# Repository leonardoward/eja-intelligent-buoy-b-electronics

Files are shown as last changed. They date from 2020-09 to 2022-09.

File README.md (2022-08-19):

# EJA Intelligent Buoy B with Ethernet - Electronic Design

Buoy B V2.0 integrates 4 main components (ESP32, LoRa, GPS and an Ethernet interface). It is a version of the previous Buoy B V1.0 but replaces the motor drivers with an Ethernet module.

This repository contains the KiCad design for the PCB of the Intelligent Buoy B. It also contains the 3D models used to visualize the design in the KiCad 3D viewer.

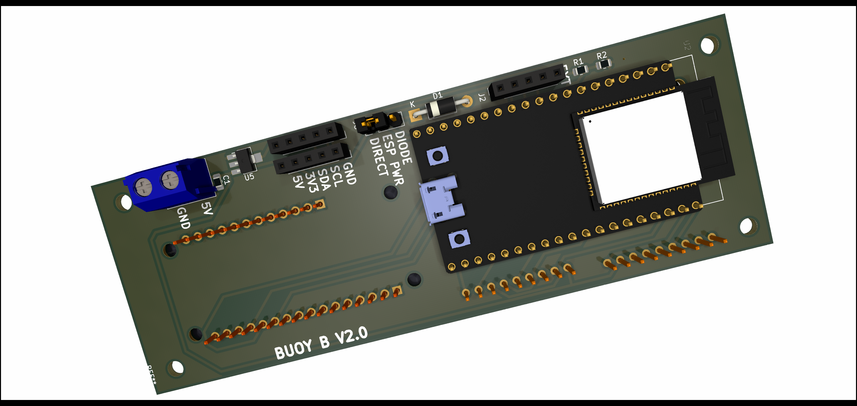
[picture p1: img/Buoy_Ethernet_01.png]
Front Layer PCB


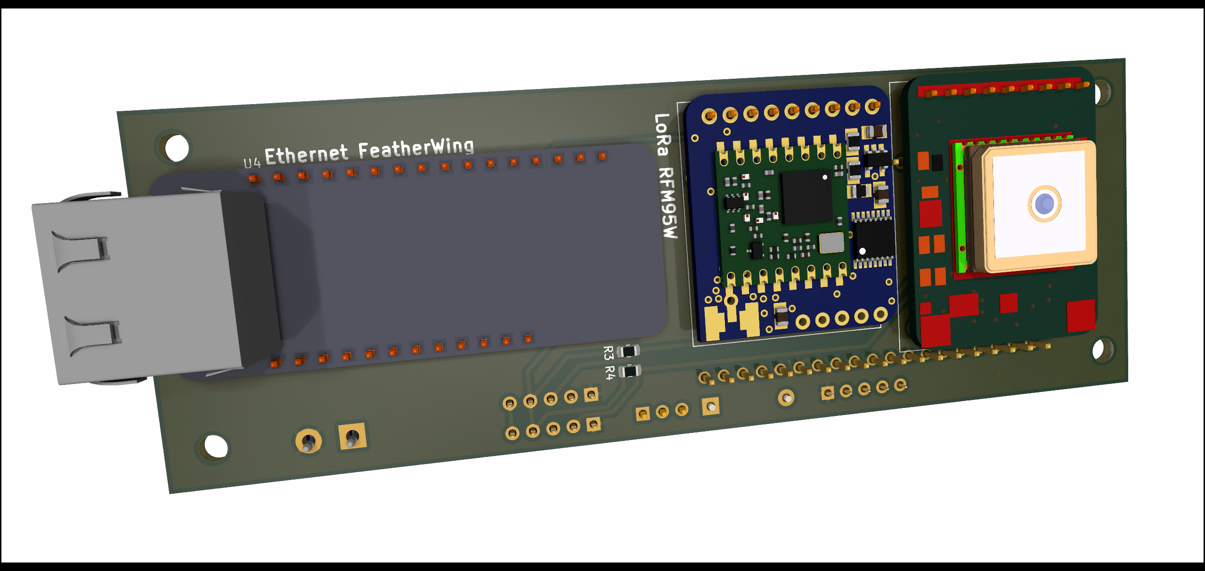
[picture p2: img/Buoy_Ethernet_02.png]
Back Layer PCB


## Main Components ##

- [ESP32-DEVKITC-32D](https://www.digikey.com/product-detail/es/espressif-systems/ESP32-DEVKITC-32D/1965-1000-ND/9356990)
- [RFM95W LoRa Radio](https://www.digikey.com/product-detail/es/adafruit-industries-llc/3072/1528-1667-ND/6005357)
- [TB6612FNG MOTOR DRIVER BOARD](https://www.digikey.com/product-detail/es/sparkfun-electronics/ROB-14450/1568-1755-ND/7915576)
- [Adafruit Ethernet FeatherWing](https://www.digikey.com/en/products/detail/adafruit-industries-llc/3201/6165788)

## Schematic ##

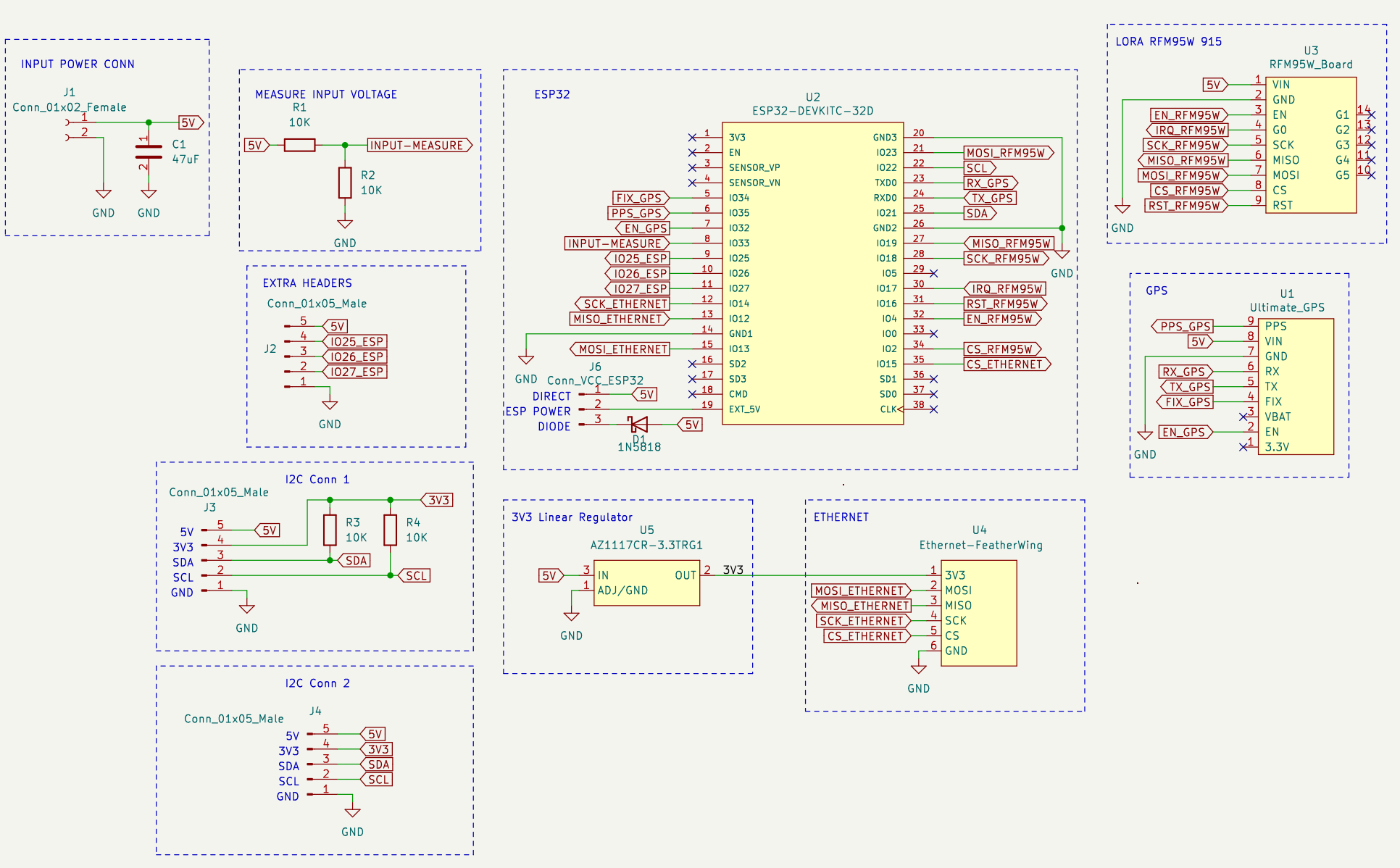
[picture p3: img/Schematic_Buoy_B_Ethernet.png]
Schematic


<!-- [For a detailed explanation of the schematic visit the following log.](https://hackaday.io/project/173457/log/181832-buoy-b-v10-schematic-and-pcb-design) -->

## PCB Layout ##

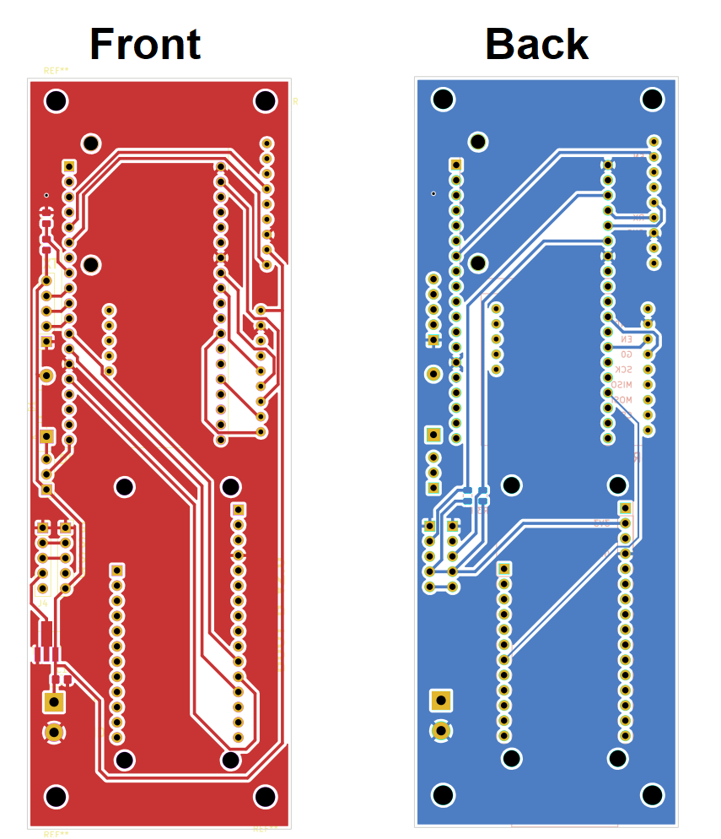
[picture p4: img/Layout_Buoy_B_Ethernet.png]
PCB Layout


## Assembly ##

Components List:

1. [ESP32-DEVKITC-32D](https://www.digikey.com/product-detail/es/espressif-systems/ESP32-DEVKITC-32D/1965-1000-ND/9356990)
2. [ETHERNET FEATHERWING](https://www.digikey.com/en/products/detail/adafruit-industries-llc/3201/6165788)
3. [CONN HDR 19POS 0.1 TIN PCB](https://www.digikey.com/product-detail/es/sullins-connector-solutions/PPTC191LFBN-RC/S7017-ND/810157)
4. [CONN HDR 9POS 0.1 GOLD PCB](https://www.digikey.com/product-detail/es/sullins-connector-solutions/PPPC091LFBN-RC/S7042-ND/810181)
5. [CONN HDR 9POS 0.1 GOLD PCB](https://www.digikey.com/product-detail/es/sullins-connector-solutions/PPPC091LFBN-RC/S7042-ND/810181)
8. PCB Buoy B V1.0
9. [CONN HDR 19POS 0.1 TIN PCB](https://www.digikey.com/product-detail/es/sullins-connector-solutions/PPTC191LFBN-RC/S7017-ND/810157)
10. [TERM BLK 2P SIDE ENT 5.08MM PCB](https://www.digikey.com/product-detail/es/on-shore-technology-inc/OSTTC022162/ED2609-ND/614558)
12. [CONN HDR 6POS 0.1 TIN PCB](https://www.digikey.com/product-detail/es/sullins-connector-solutions/PPTC061LFBN-RC/S7004-ND/810145)
13. [CONN HDR 5POS 0.1 GOLD PCB](https://www.digikey.com/product-detail/es/sullins-connector-solutions/PPTC051LFBN-RC/S6103-ND/807239)
14. [CONN HEADER VERT 3POS 2.54MM](https://www.digikey.com/product-detail/es/jst-sales-america-inc/S2B-XH-A-1-LF-SN/455-4226-ND/9961922)
15. [CONN HEADER VERT 3POS 2.54MM](https://www.digikey.com/product-detail/es/jst-sales-america-inc/S2B-XH-A-1-LF-SN/455-4226-ND/9961922)
16. [CONN HEADER R/A 3POS 2.5MM](https://www.digikey.com/product-detail/es/jst-sales-america-inc/S3B-XH-A-1-LF-SN/455-2954-ND/1556255)
17. Coin cell holder (included in [Adafruit Ultimate GPS](https://www.digikey.com/product-detail/es/adafruit-industries-llc/746/1528-1153-ND/5353613))
18. [Adafruit Ultimate GPS](https://www.digikey.com/product-detail/es/adafruit-industries-llc/746/1528-1153-ND/5353613)
19. CONN HDR 16POS 0.1 TIN PCB (included in [Adafruit Ultimate GPS](https://www.digikey.com/product-detail/es/adafruit-industries-llc/746/1528-1153-ND/5353613))
20. [RFM95W LoRa Radio](https://www.digikey.com/product-detail/es/adafruit-industries-llc/3072/1528-1667-ND/6005357)
21. CONN HEADER VERT 16POS 2.54MM (included in [RFM95W LoRa Radio](https://www.digikey.com/product-detail/es/adafruit-industries-llc/3072/1528-1667-ND/6005357))

<!-- [For a detailed Bill of Materials visit the following log.](https://hackaday.io/project/173457/log/183762-buoy-b-v10-bill-of-materials)

[For a detailed explanation about the soldering and assembly procedure visit the following log.](https://hackaday.io/project/173457/log/183666-buoy-b-v10-assembly) -->

<!-- ## Wiring Diagrams ##

### Battery Management ###

The original design of the board considered the following components:

- Battery (5V < Voltage < 15V)
- PCB Board Buoy B V1.0
- Buck Converter
- Switch
- Extra capacitor

![alt text](./Wiring_Diagrams/Wiring_Buoy_WithoutGSM_07_wired.png "Buck Converter")

Also, there is an alternative for the battery management, is possible to provide the required voltages with a boost converter and a 3.7V Battery, like the following example:

- 3.7V 1 Cell Battery
- PCB Board Buoy B V1.0
- Boost Converter
- Micro USB Breakout Board
- Switch
- Extra capacitor
- JST-XH 2 Pos female connector and a JST-XH 2 Pos male connector
- 5V Charger (only used to charge the battery)

![alt text](./Wiring_Diagrams/Wiring_Buoy_WithoutGSM_08_wired.png "Boost Converter")

This alternative is valid and possible, but is not ideal for longer working time (compared to the first one). It is important to consider the efficiency of the boost converter. The selected boost converter will have a voltage drop at a current higher than 500mA, that should be taken into consideration.

### Motors ###

The board was designed to handle 3 different types of motors, those are:

- Servo Motor

![alt text](./Wiring_Diagrams/Wiring_Buoy_WithoutGSM_06_wired.png "Servo Motor")

- Stepper Motor (using the driver TB6612FNG)

![alt text](./Wiring_Diagrams/Wiring_Buoy_WithoutGSM_09_wired.png "Stepper Motor")

- DC Motor (using the driver TB6612FNG)

![alt text](./Wiring_Diagrams/Wiring_Buoy_WithoutGSM_05_wired.png "DC Motor 1")

![alt text](./Wiring_Diagrams/Wiring_Buoy_WithoutGSM_05_wired_2.png "DC Motor 2")

[For more information about the wiring diagrams and the project visit the following log.](https://hackaday.io/project/173457/log/182722-buoy-b-v10-wiring-diagrams)

## Future improvements ##

[For more information about the recommended future improvements for the electronic design visit the following log.](https://hackaday.io/project/173457/log/183807-future-improvements-pcb-design) -->

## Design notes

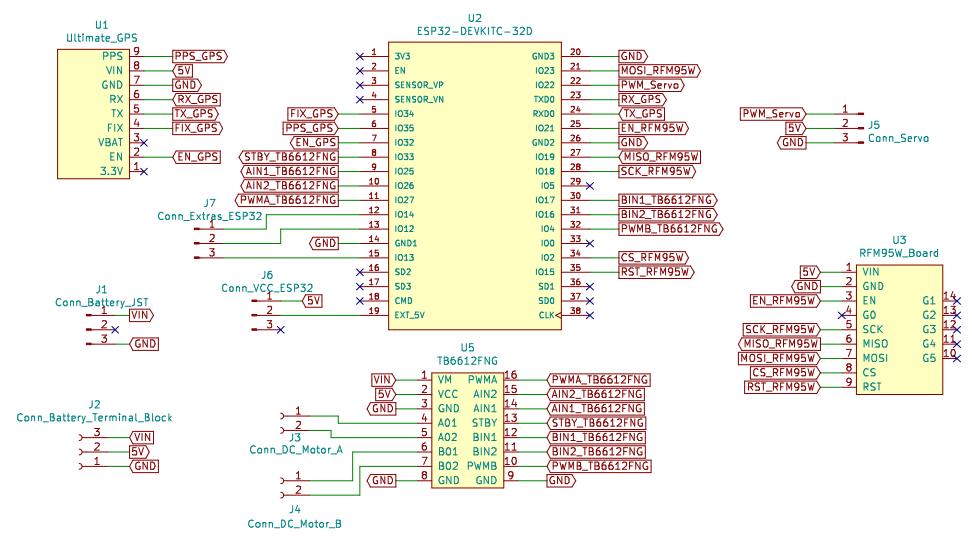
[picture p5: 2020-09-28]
img/Schematic_Buoy_B.png

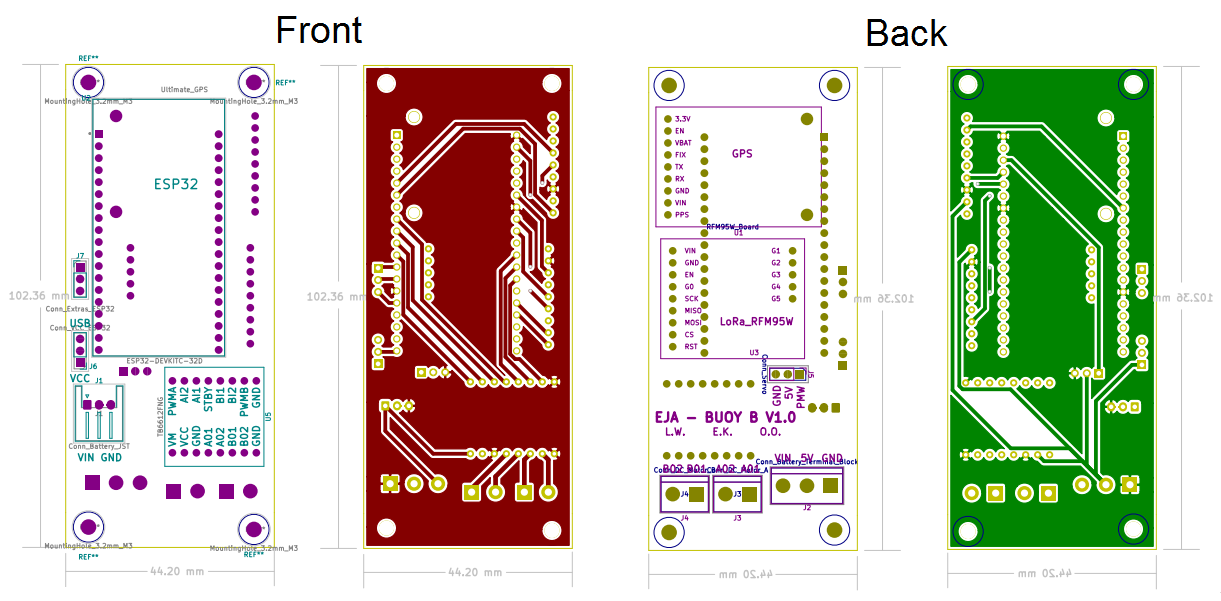
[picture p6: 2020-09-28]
img/Layout_Buoy_B.png

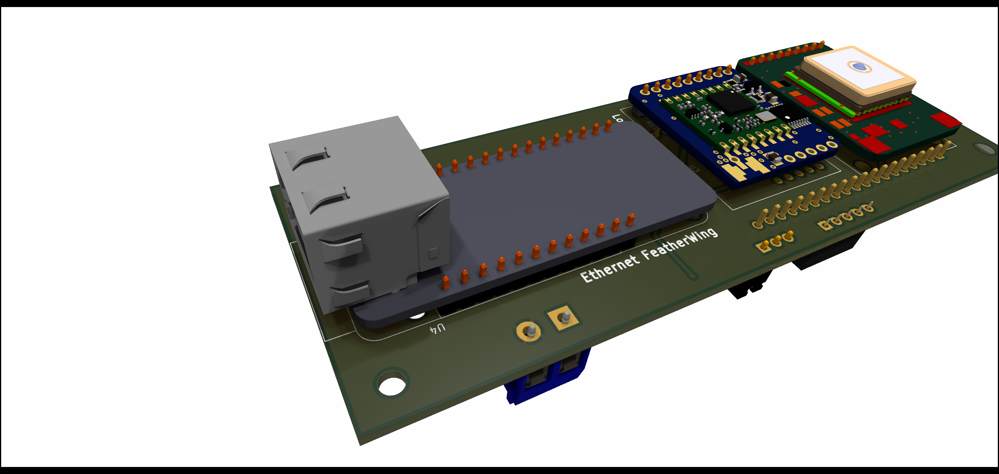
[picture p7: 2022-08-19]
img/Buoy_Ethernet_03.png

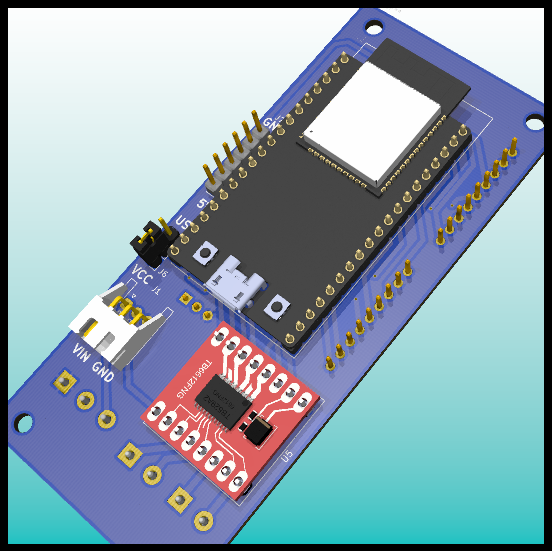
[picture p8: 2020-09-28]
img/Buoy_B_WithoutGSM_01.png

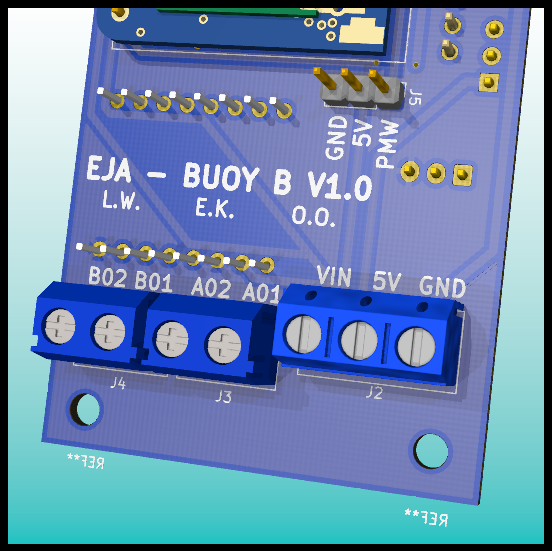
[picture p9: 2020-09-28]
img/Buoy_B_WithoutGSM_08.png

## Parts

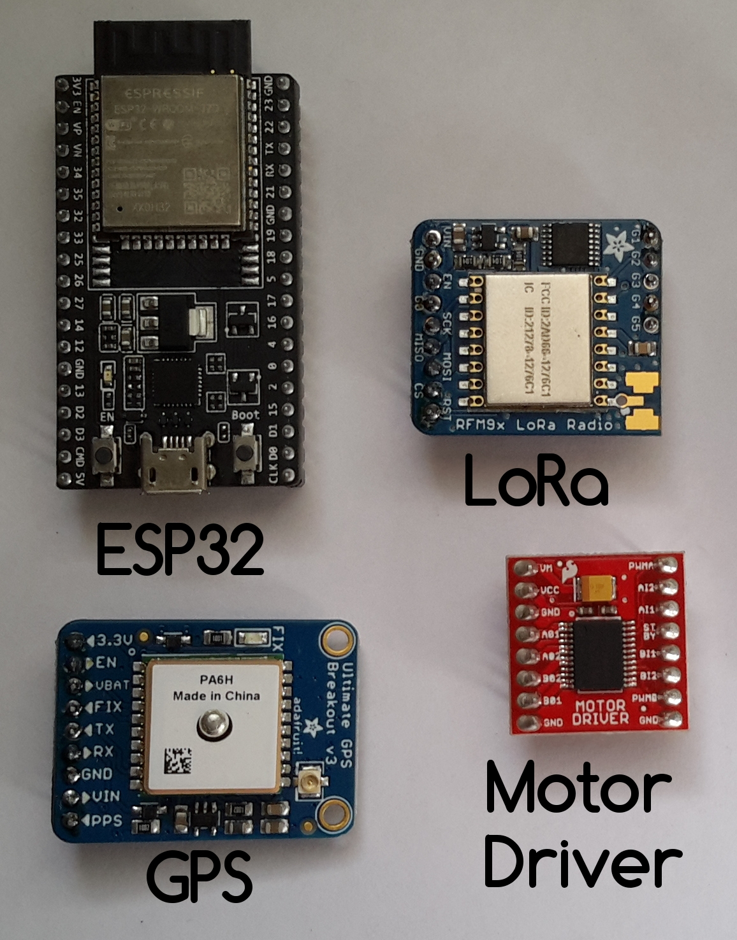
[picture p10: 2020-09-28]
img/Components_Buoy_B.jpg

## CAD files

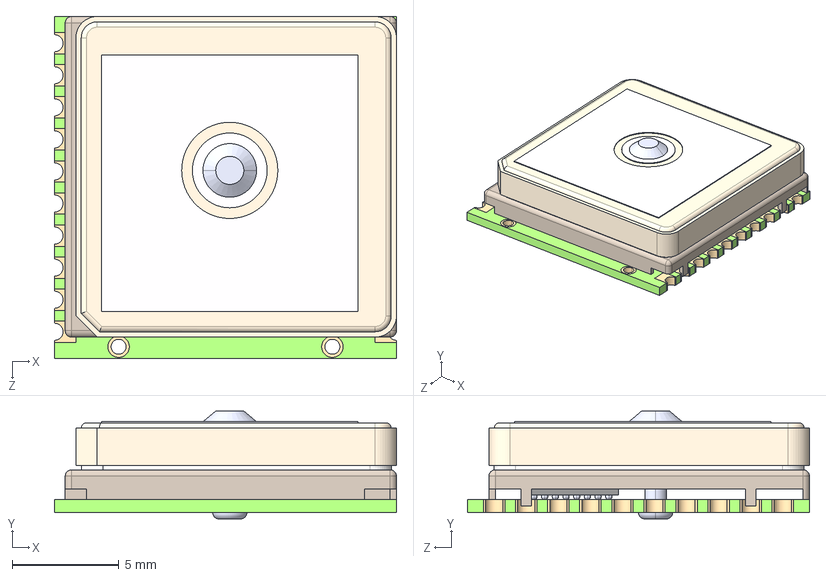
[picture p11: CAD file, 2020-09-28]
3D/PA6H Assembly.STEP
16.0 x 5.05 x 16.0 mm
PCB
VFBGA-64
RF Shield
Adhesive Pad
Ceramic Antenna
Rivet

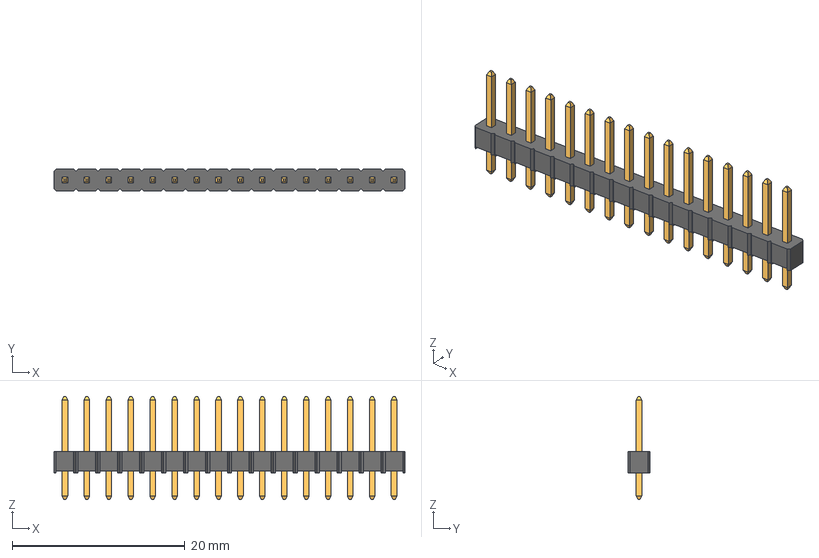
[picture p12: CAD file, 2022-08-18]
3D/16-Pin Header - Male - 2.54mm.step
40.6 x 2.54 x 11.9 mm

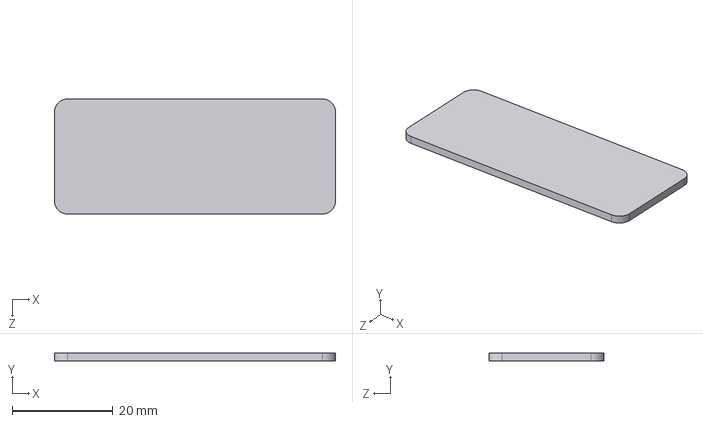
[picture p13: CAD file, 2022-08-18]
3D/Ethernet FeatherWing PCB.STEP
55.9 x 1.60 x 22.9 mm

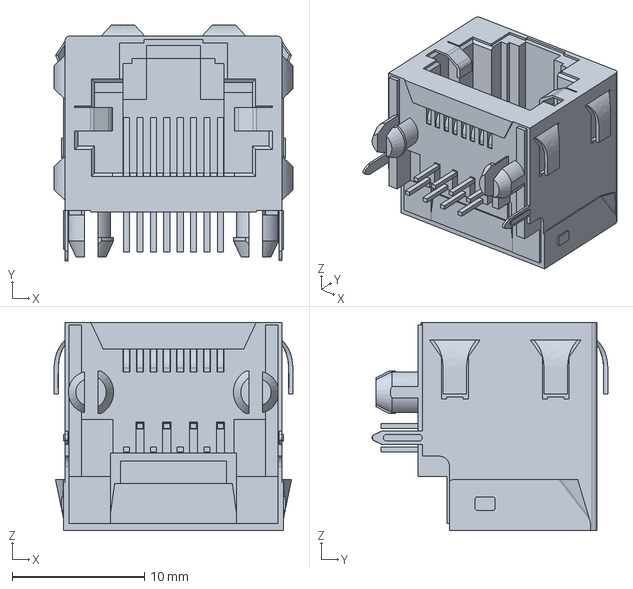
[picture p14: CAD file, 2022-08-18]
3D/ethernet connector.stp
18.0 x 17.8 x 15.7 mm

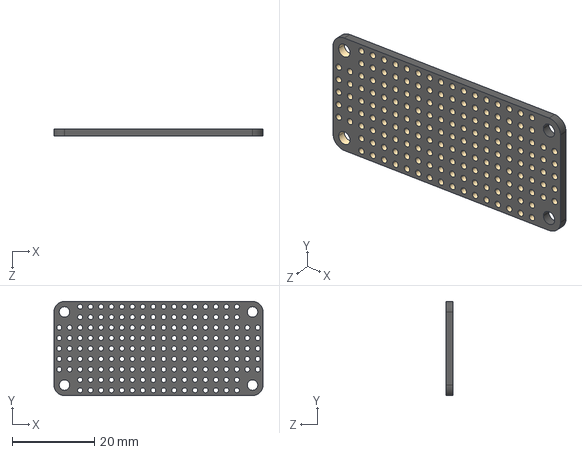
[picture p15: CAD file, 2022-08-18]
3D/FeatherWing Proto1.STEP
50.8 x 22.9 x 1.60 mm

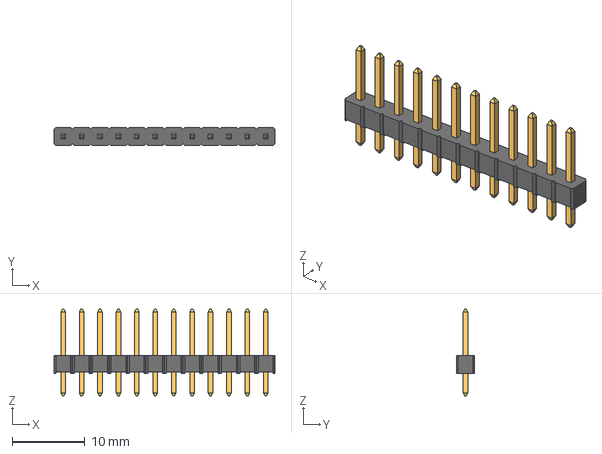
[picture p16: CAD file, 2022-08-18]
3D/12-Pin Header - Male - 2.54mm.step
30.5 x 2.54 x 11.9 mm

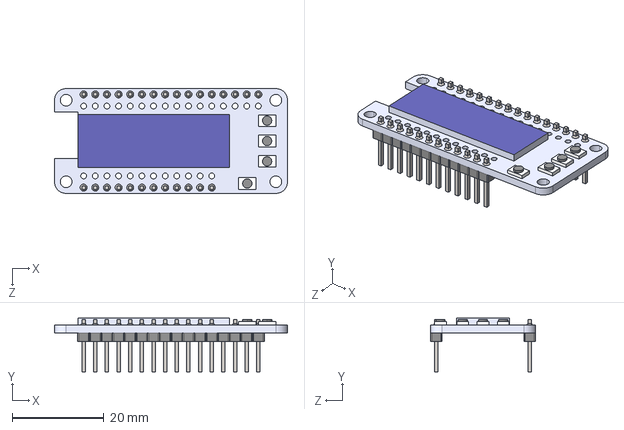
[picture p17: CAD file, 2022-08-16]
3D/Adafruit_Feather_Display032x128_000.STEP
50.8 x 11.7 x 22.9 mm

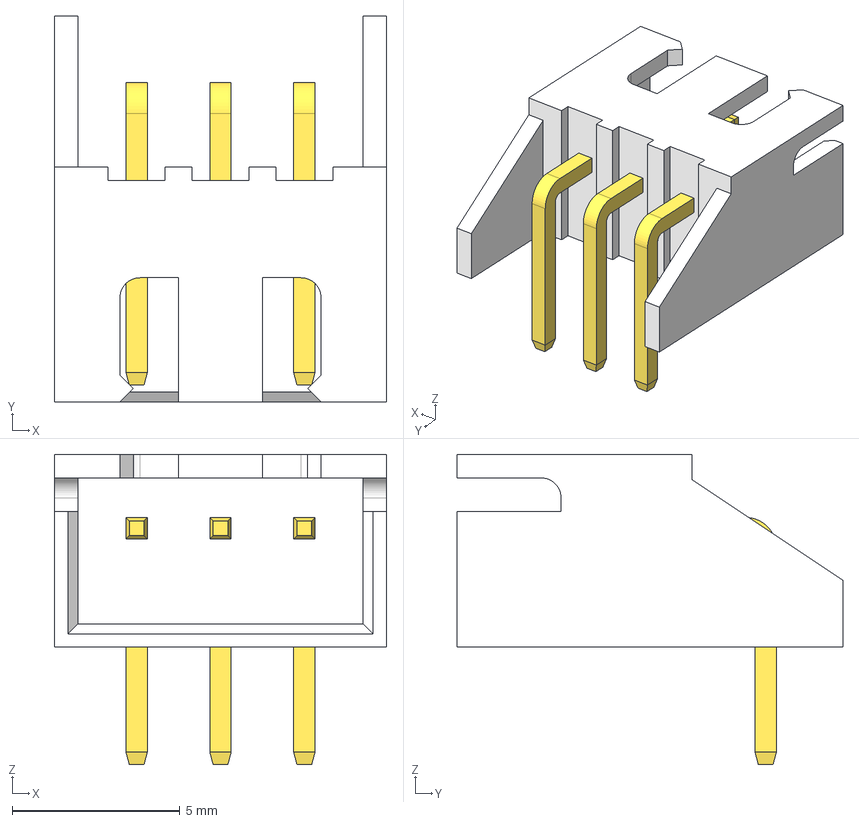
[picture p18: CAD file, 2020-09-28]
3D/S3B-XH-A.step
9.90 x 11.5 x 9.25 mm

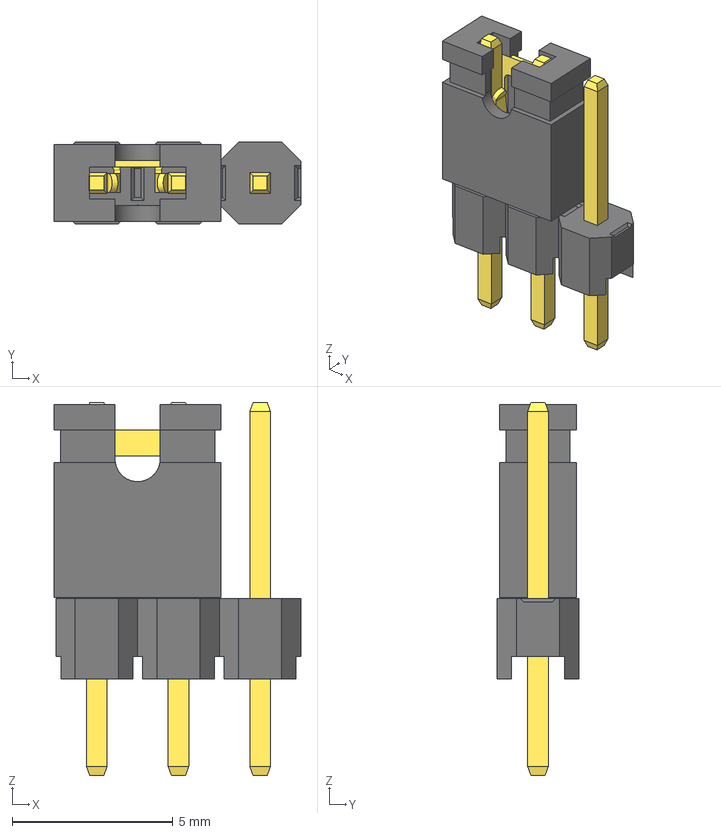
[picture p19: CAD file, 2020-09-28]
3D/Jumper3.step
7.68 x 2.54 x 11.6 mm

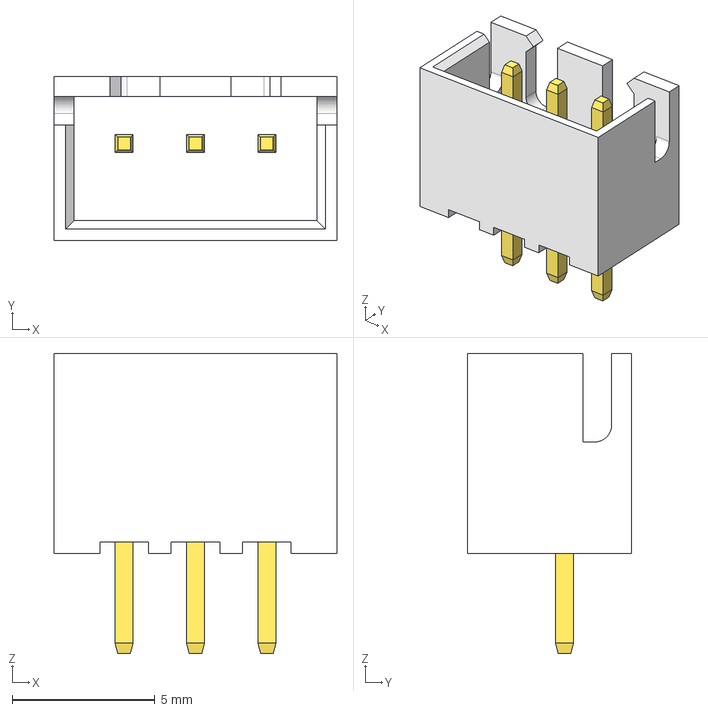
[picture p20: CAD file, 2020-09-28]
3D/B3B-XH-A.step
9.90 x 5.75 x 10.5 mm

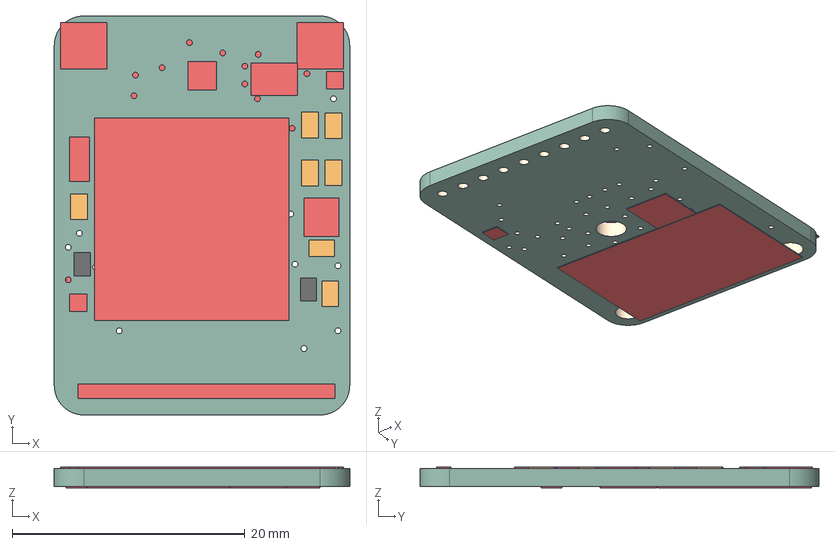
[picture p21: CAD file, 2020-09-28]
3D/Adafruit Ultimate GPS.step
25.4 x 34.3 x 1.77 mm
Board
FGPMMOPA6H
MIC5225-3.3
RED
10K x 7
MOUNTINGHOLE2.5 x 2
CUS520 x 2
CR1220
FIDUCIAL"" x 2
ADAFRUIT_2.5MM
U.FL
1X09_ROUND_70
PCBFEAT-REV-040
ADAFRUIT_5MM

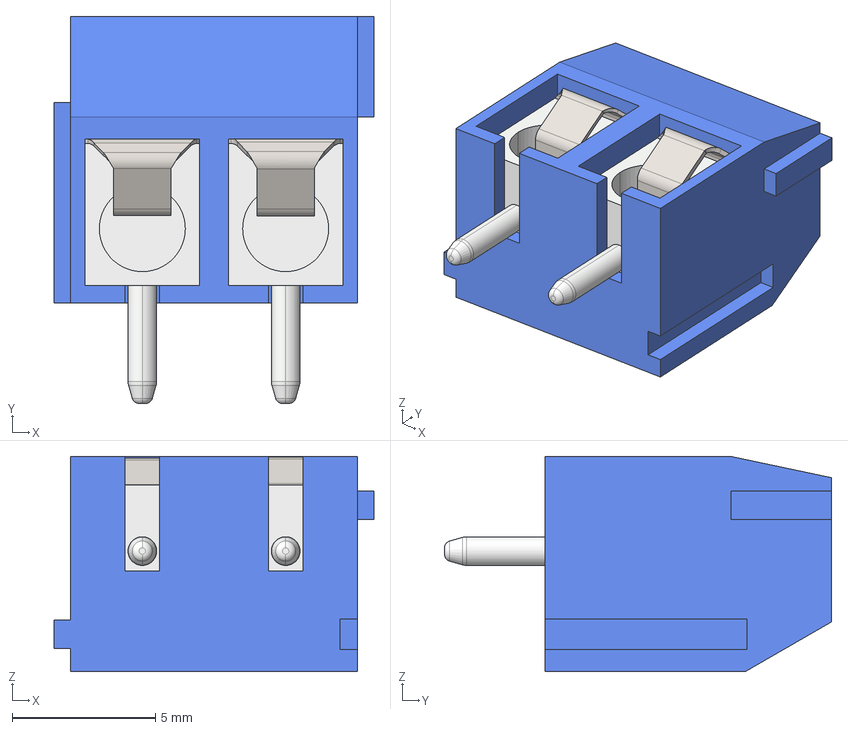
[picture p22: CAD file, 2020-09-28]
3D/TE_1776244-2.STEP
11.2 x 13.5 x 7.50 mm

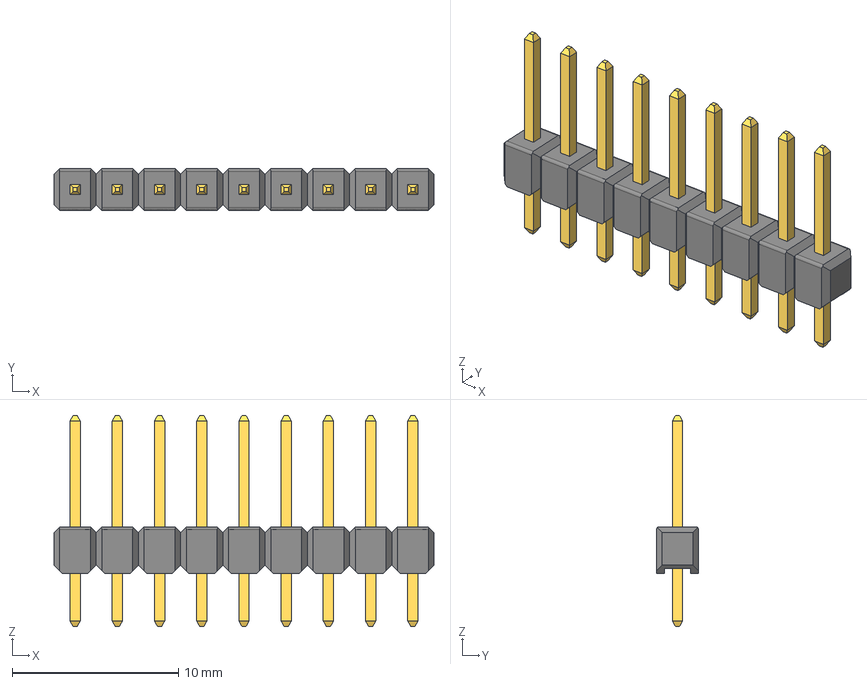
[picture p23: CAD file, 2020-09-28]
3D/Pin Header 1x9 TH Pitch 2.54mm.stp
22.9 x 2.54 x 12.7 mm

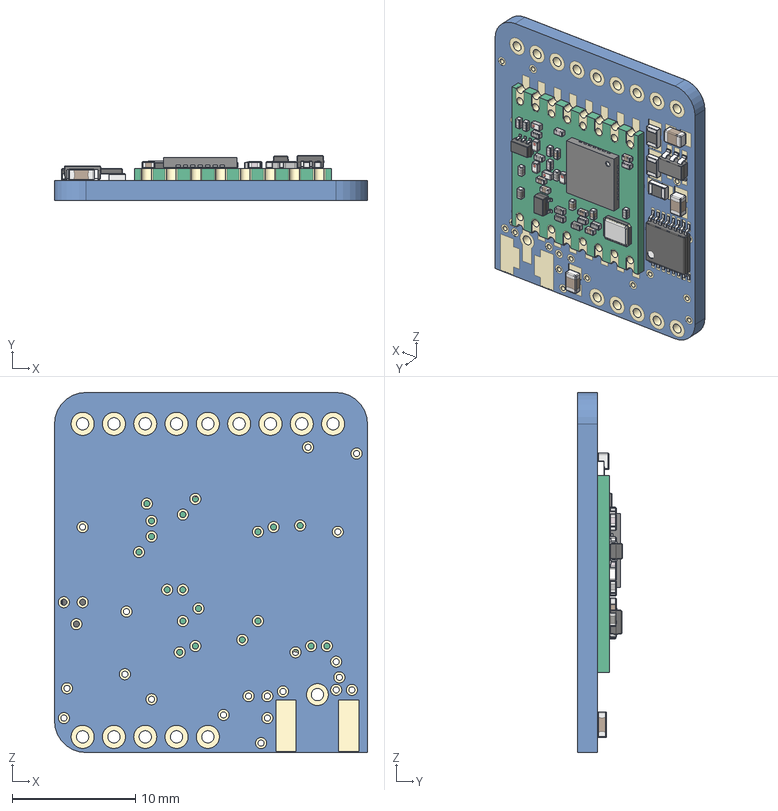
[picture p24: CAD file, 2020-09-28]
3D/RFM95W v5.step
25.4 x 3.63 x 29.2 mm
QFN 28 v2
SMD Crystal v1
CAP 0403 v1 x 8
CAP Ceramic 0403 v1 x 8
Res 0403 v1 x 4
CAP ML 0403 v1 x 5
SOT-323 v1
Inductor SMD 0403 v1 x 5
SOT-363 v1
SOT23-5
CAP 0805 T095 x 2
CAP 0805 T075
TSSOP16
RES 0805 x 3

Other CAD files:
3D/Pin Header 1x4 TH Pitch 2.54mm.stp
3D/terminal_block_tb5p-3p_p5_l15_w7-6_h10.stp
3D/Pin Header 1x6 TH Pitch 2.54mm.stp
3D/Pin Header 1x3 TH Pitch 2.54mm.stp
3D/Pin Header 1x5 TH Pitch 2.54mm.stp

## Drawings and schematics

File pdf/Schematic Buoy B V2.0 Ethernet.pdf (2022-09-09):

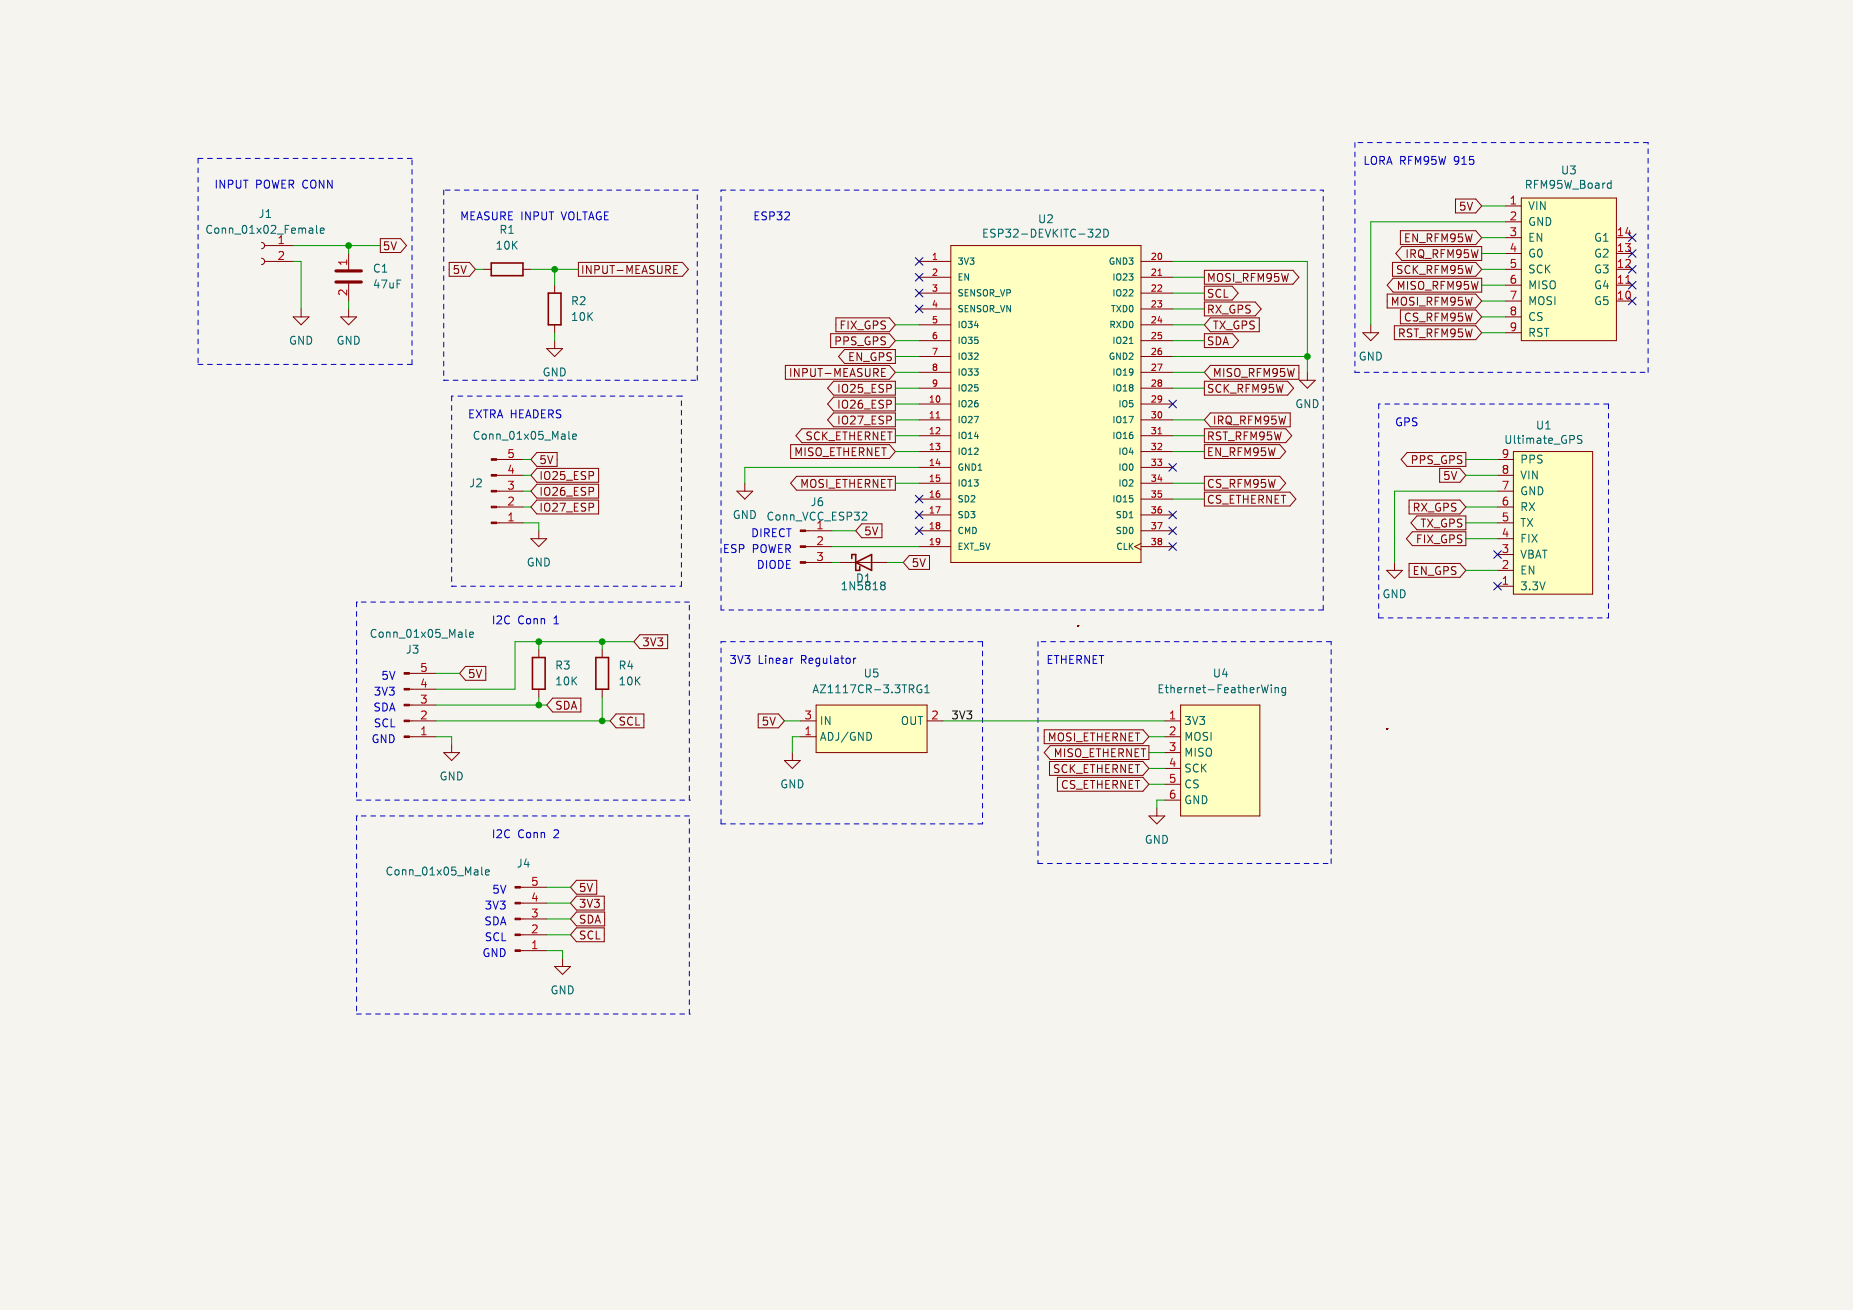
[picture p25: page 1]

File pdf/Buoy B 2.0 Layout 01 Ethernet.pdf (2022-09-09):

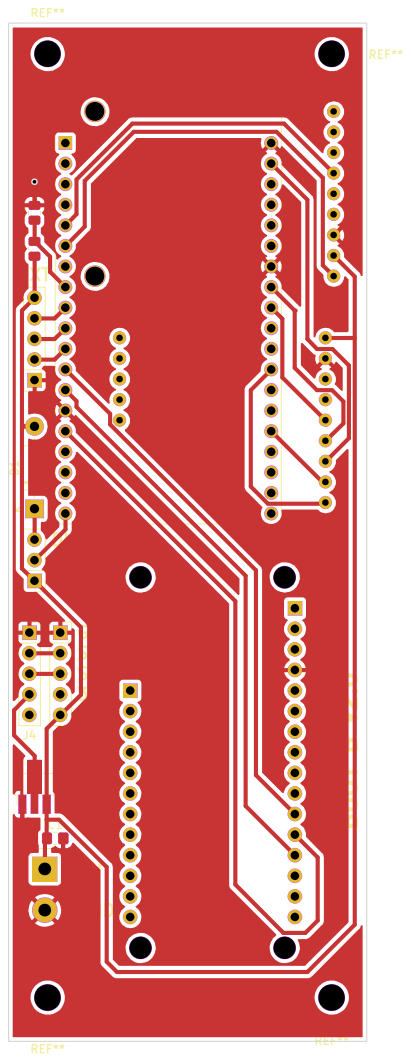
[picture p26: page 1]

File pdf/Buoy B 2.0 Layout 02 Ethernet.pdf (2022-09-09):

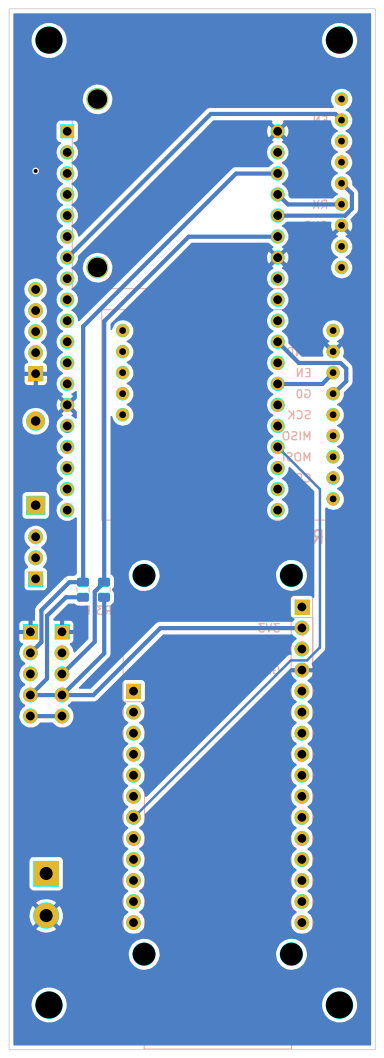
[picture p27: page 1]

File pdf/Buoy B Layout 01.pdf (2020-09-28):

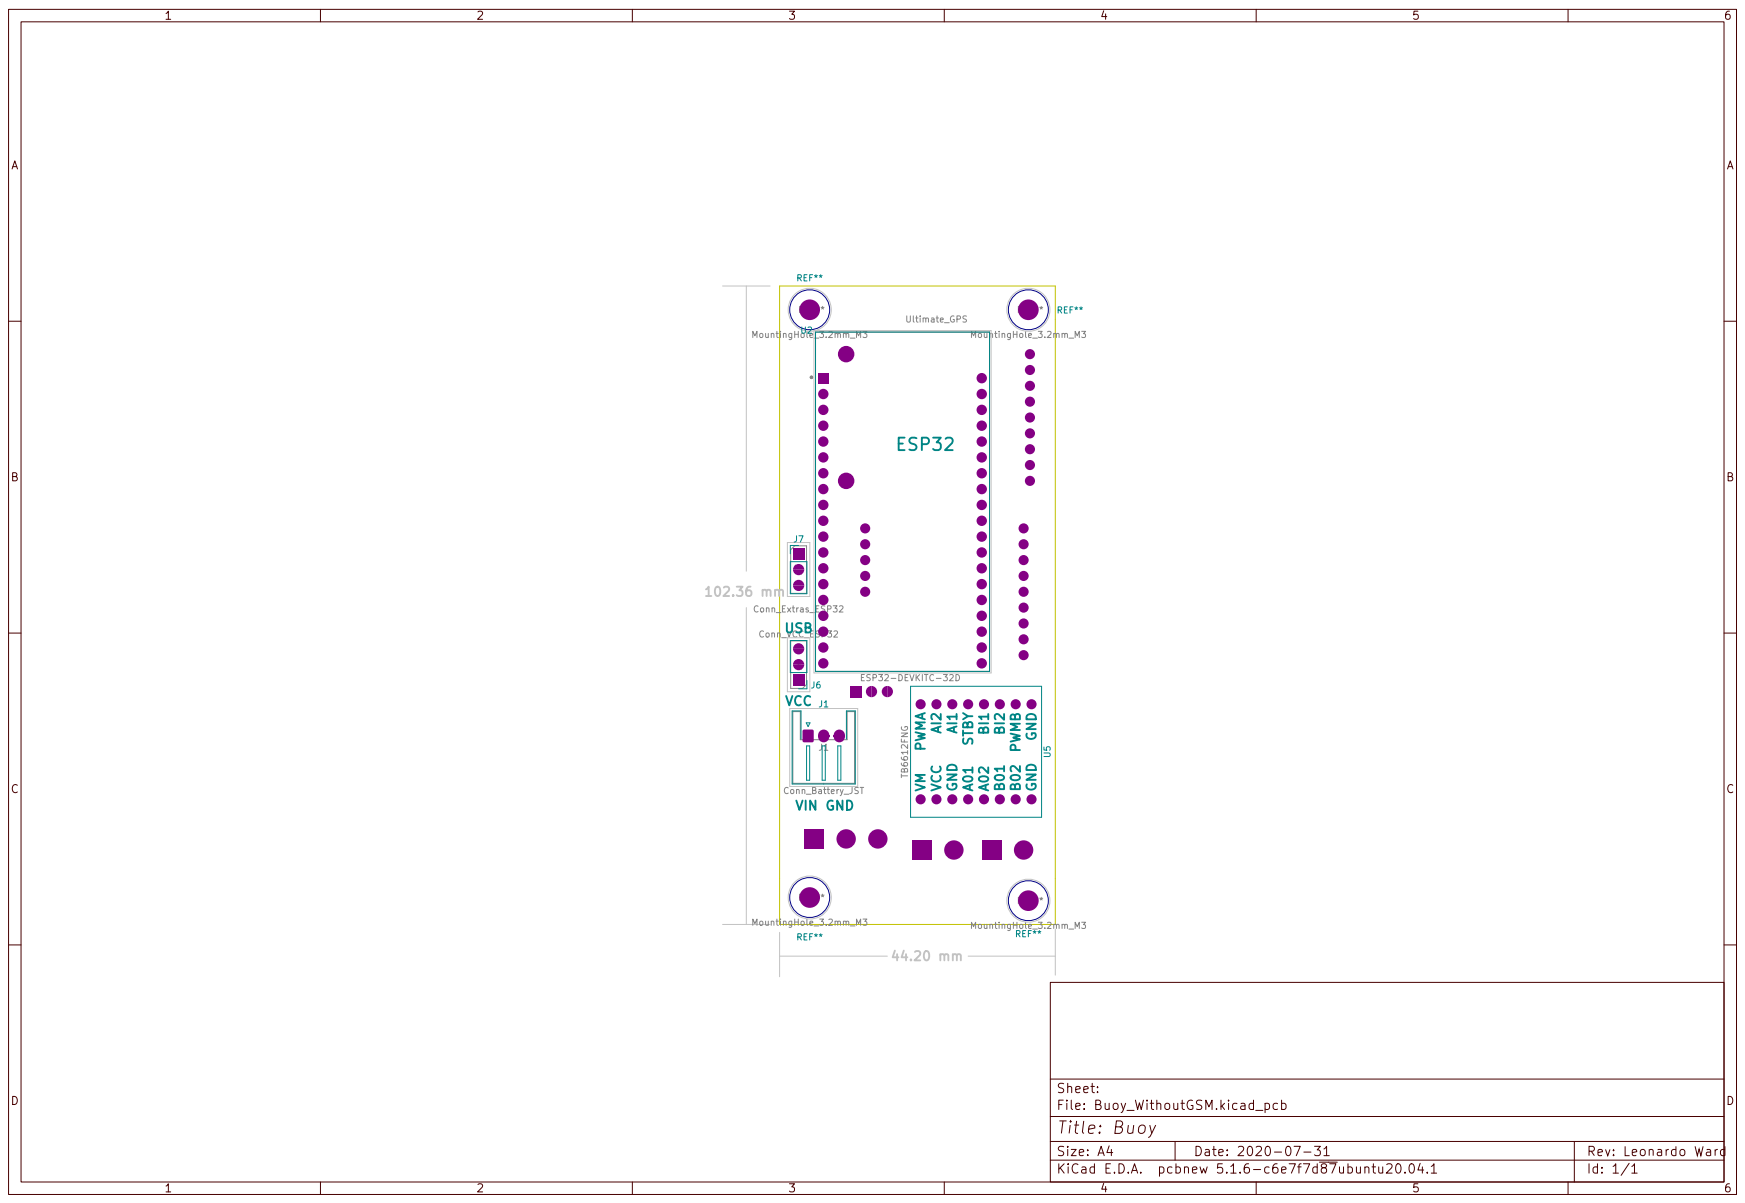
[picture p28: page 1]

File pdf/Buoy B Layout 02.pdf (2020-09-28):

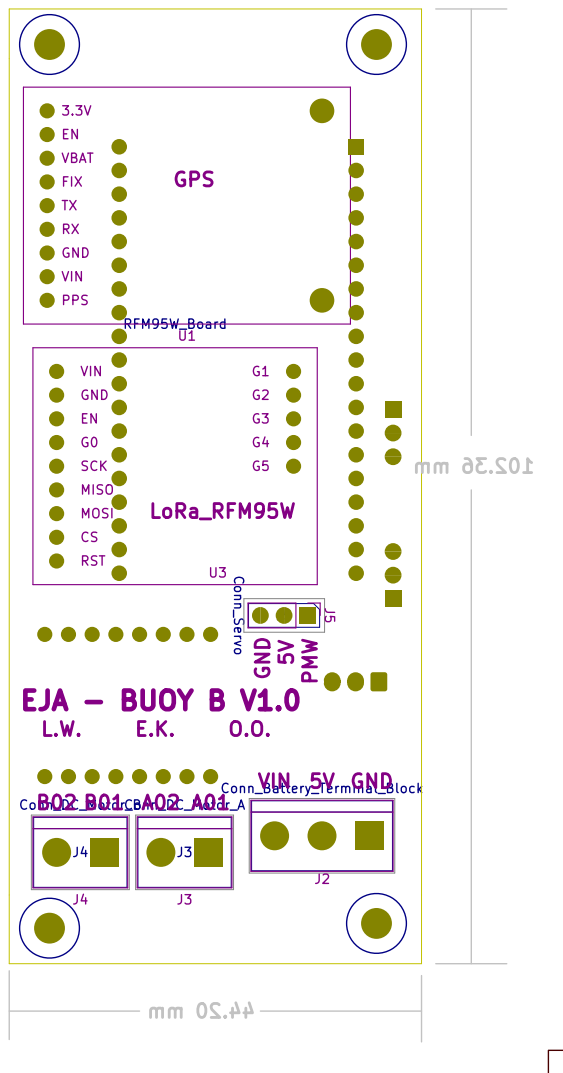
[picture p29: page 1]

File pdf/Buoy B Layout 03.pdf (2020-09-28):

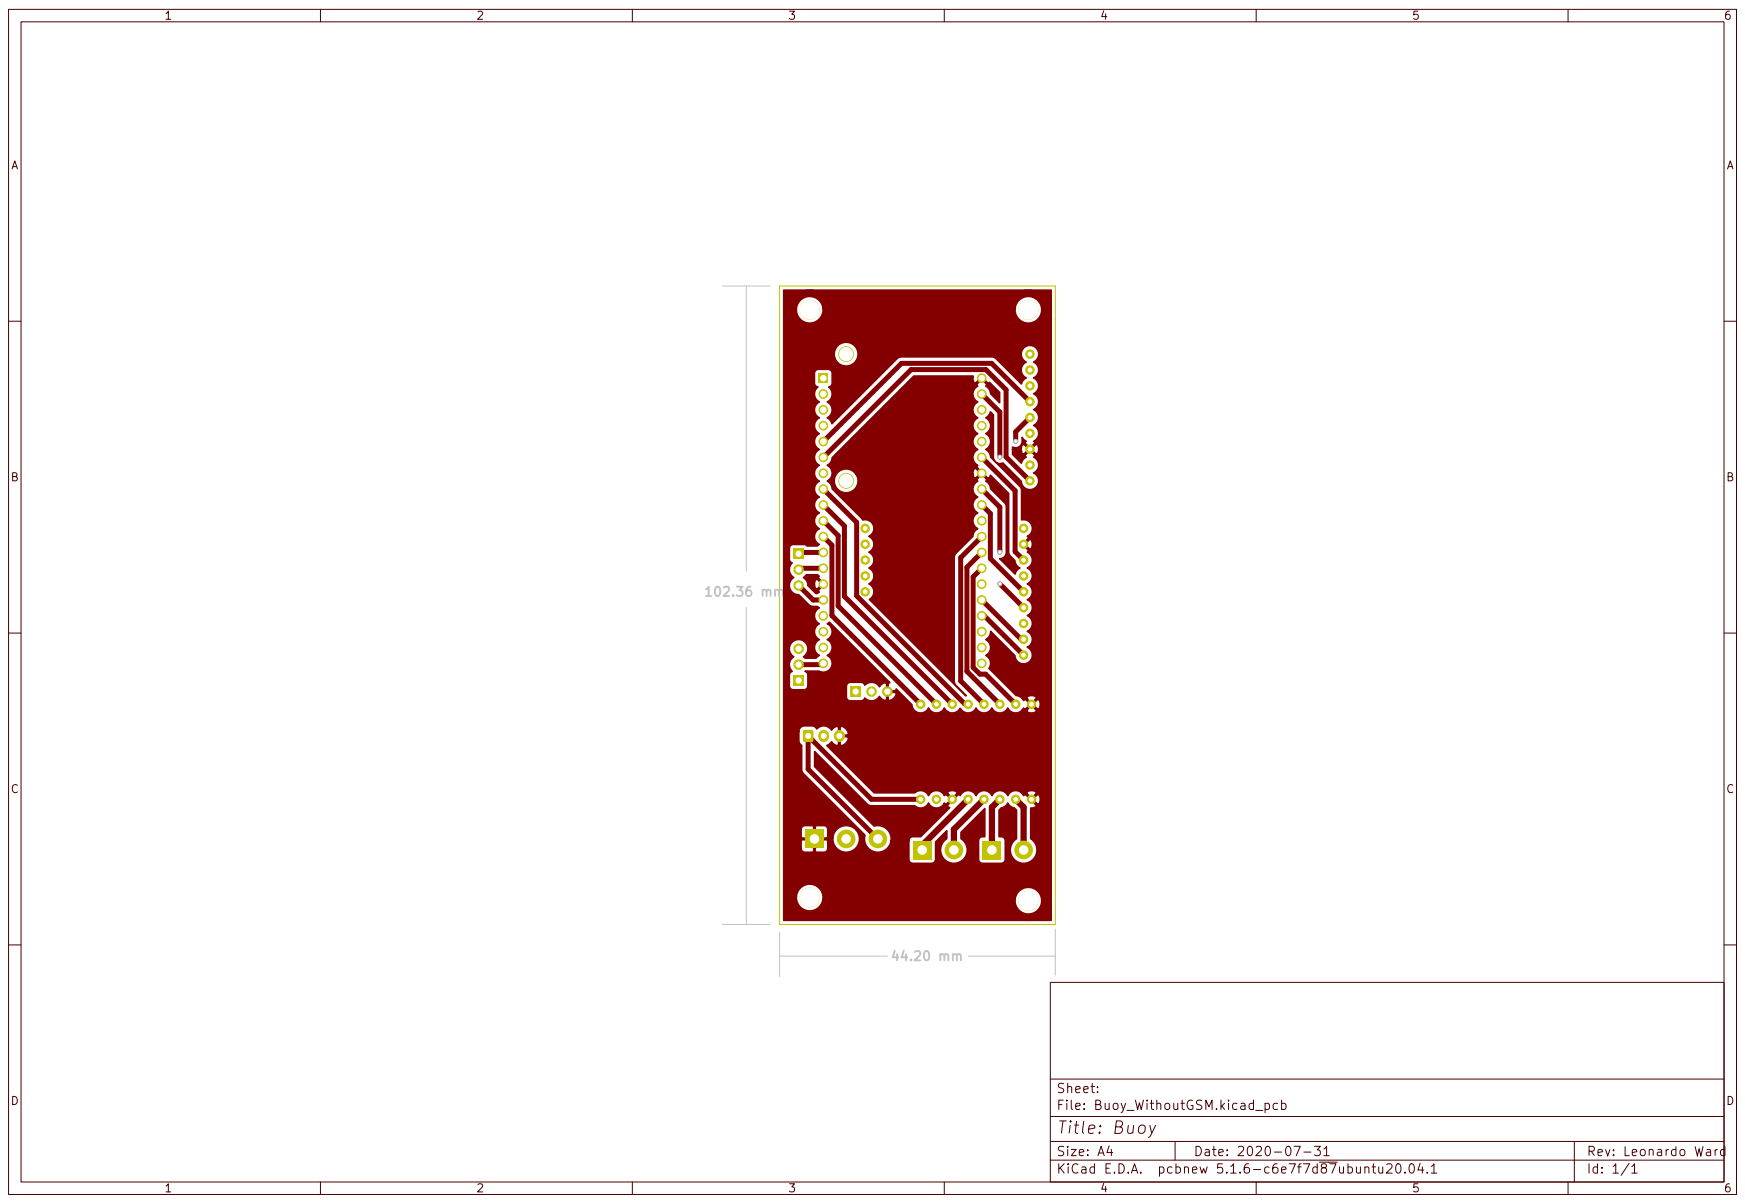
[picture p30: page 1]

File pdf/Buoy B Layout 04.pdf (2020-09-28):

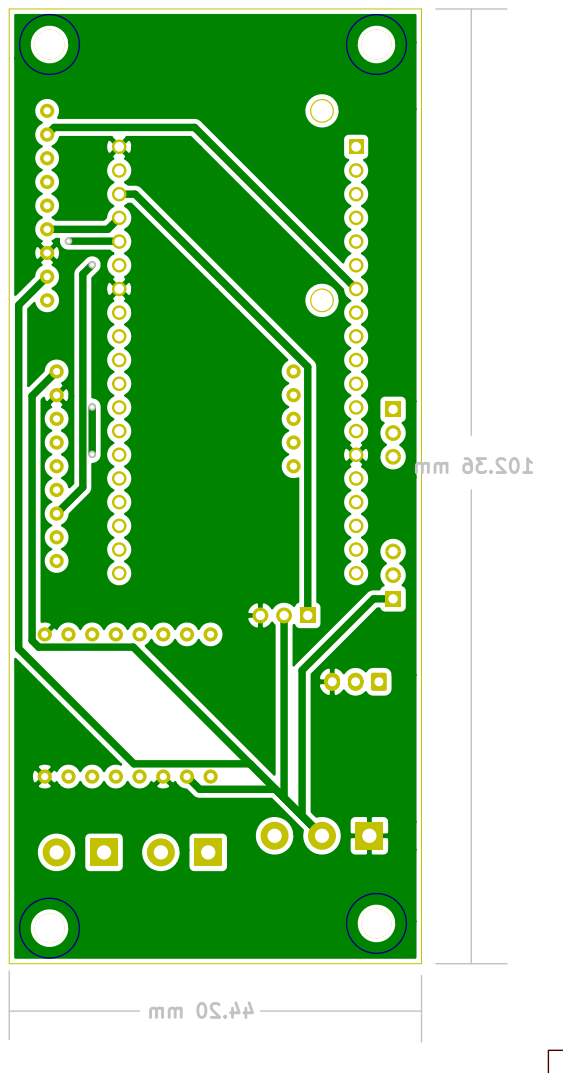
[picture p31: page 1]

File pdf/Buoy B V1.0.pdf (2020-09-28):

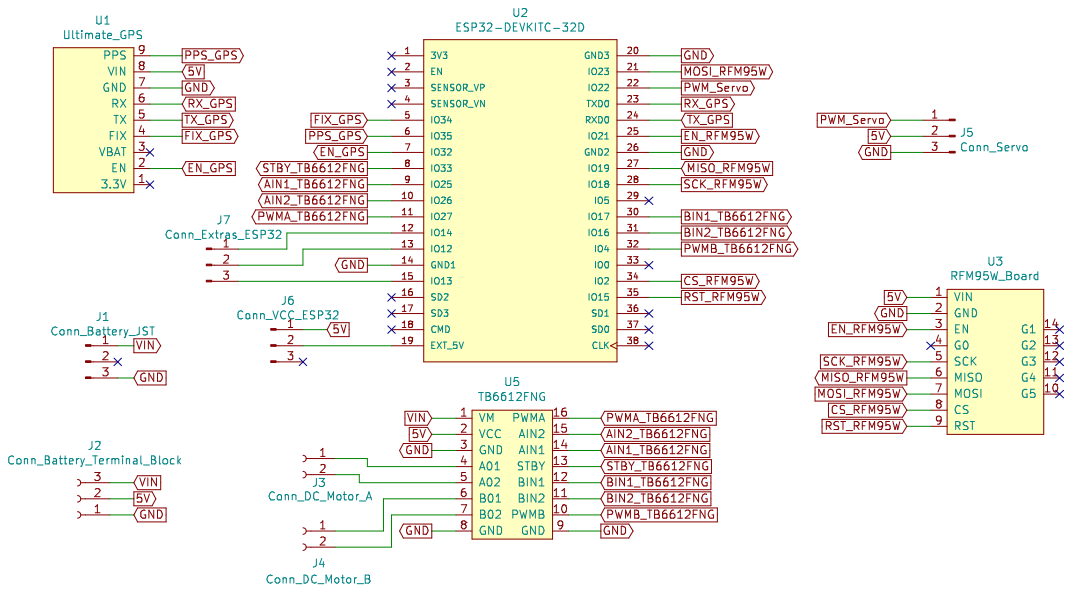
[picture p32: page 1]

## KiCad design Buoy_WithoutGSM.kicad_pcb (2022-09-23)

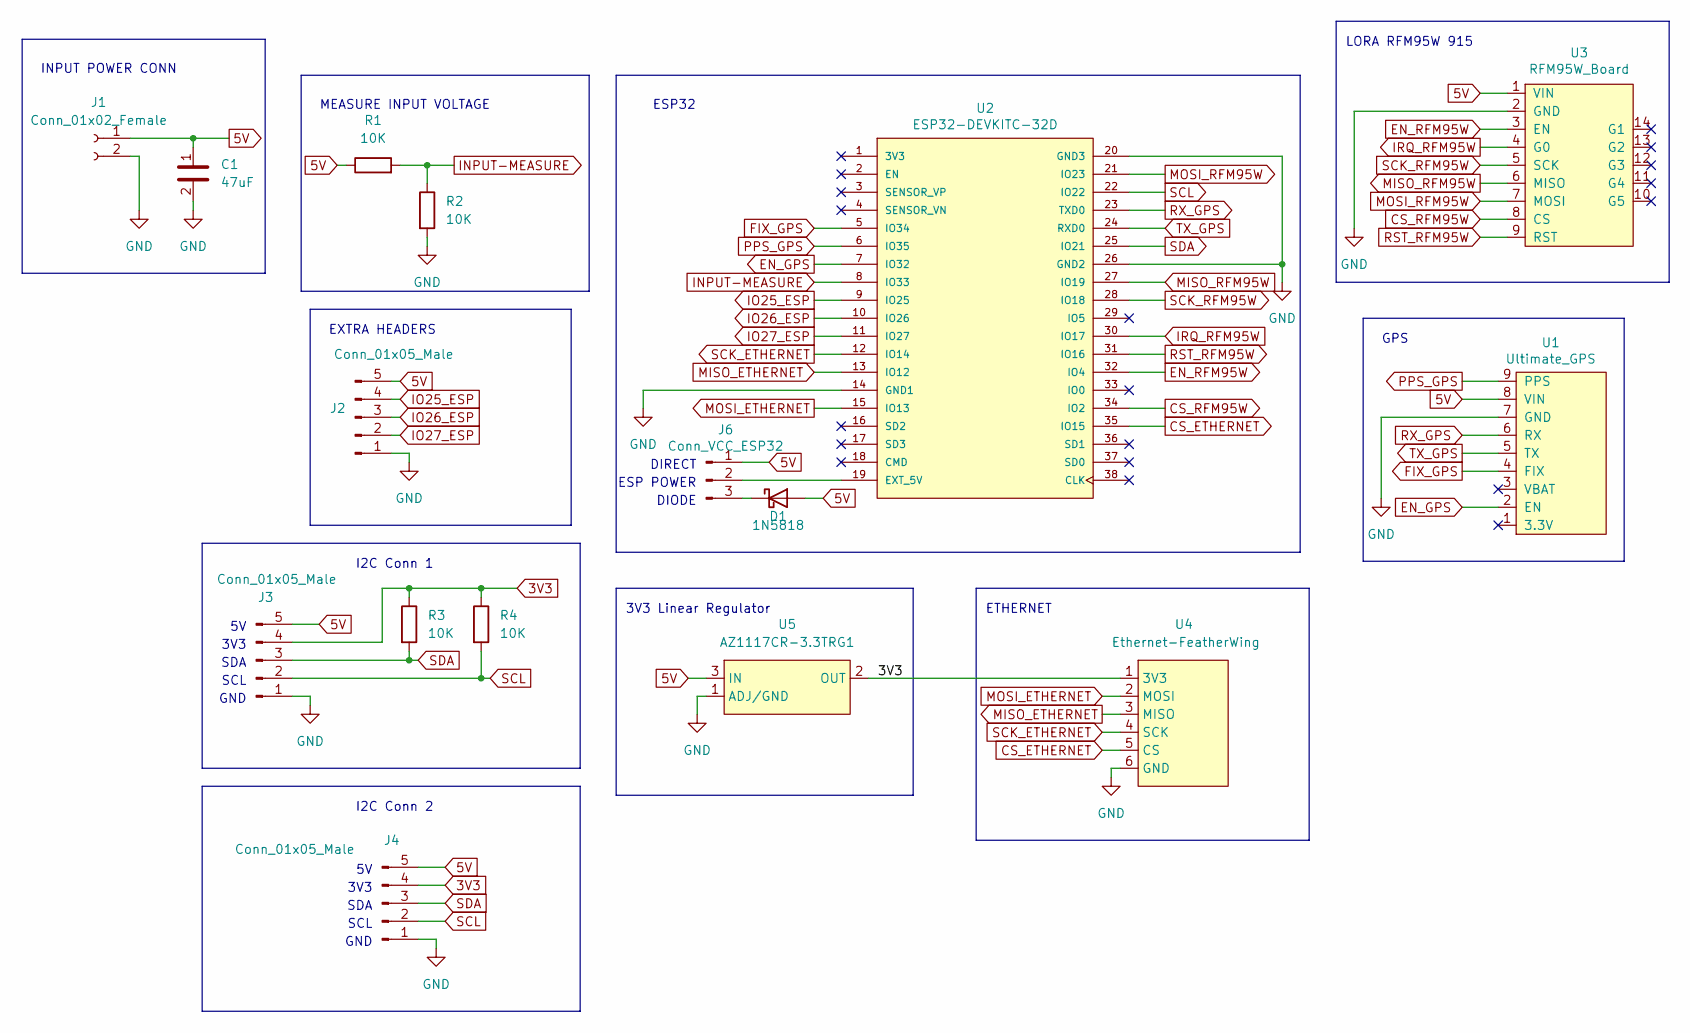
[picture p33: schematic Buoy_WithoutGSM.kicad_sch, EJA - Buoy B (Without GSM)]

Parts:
C1: 47uF; R_0805_2012Metric_Pad1.20x1.40mm_HandSolder; Manufacturer_Part_Number LMK212BBJ476MG-T
D1: 1N5818; D_DO-41_SOD81_P10.16mm_Horizontal
J1: Conn_01x02_Female; TerminalBlock_bornier-2_P5.08mm
J2, J3, J4: Conn_01x05_Male; PinSocket_1x05_P2.54mm_Vertical
J6: Conn_VCC_ESP32; PinHeader_1x03_P2.54mm_Vertical
R1, R2, R3, R4: 10K; R_0805_2012Metric; Manufacturer_Part_Number CRCW080510K0FKEAC
U1: Ultimate_GPS
U2: ESP32-DEVKITC-32D; MODULE_ESP32-DEVKITC-32D
U3: RFM95W_Board; RFM95W-Board
U4: Ethernet-FeatherWing; Ethernet FeatherWing; Manufacturer Part Number 3201
U5: AZ1117CR-3.3TRG1; SOT-89-3_Handsoldering; Manufacturer_Part_Name AZ1117CR-3.3TRG1

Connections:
3V3: J3.4, J4.4, R3.1, R4.1, U4.1 (3V3), U5.2 (OUT)
5V: C1.1, D1.2 (A), J1.1, J2.5, J3.5, J4.5, J6.1, R1.1, U1.8 (VIN), U3.1 (VIN), U5.3 (IN)
CS_ETHERNET: U2.35 (IO15), U4.5 (CS)
CS_RFM95W: U2.34 (IO2), U3.8 (CS)
EN_GPS: U1.2 (EN), U2.7 (IO32)
EN_RFM95W: U2.32 (IO4), U3.3 (EN)
FIX_GPS: U1.4 (FIX), U2.5 (IO34)
GND: C1.2, J1.2, J2.1, J3.1, J4.1, R2.2, U1.7 (GND), U2.14 (GND1), U2.20 (GND3), U2.26 (GND2), U3.2 (GND), U4.6 (GND), U5.1 (ADJ/GND)
INPUT-MEASURE: R1.2, R2.1, U2.8 (IO33)
IO25_ESP: J2.4, U2.9 (IO25)
IO26_ESP: J2.3, U2.10 (IO26)
IO27_ESP: J2.2, U2.11 (IO27)
IRQ_RFM95W: U2.30 (IO17), U3.4 (G0)
MISO_ETHERNET: U2.13 (IO12), U4.3 (MISO)
MISO_RFM95W: U2.27 (IO19), U3.6 (MISO)
MOSI_ETHERNET: U2.15 (IO13), U4.2 (MOSI)
MOSI_RFM95W: U2.21 (IO23), U3.7 (MOSI)
unnamed: D1.1 (K), J6.3
unnamed: J6.2, U2.19 (EXT_5V)
PPS_GPS: U1.9 (PPS), U2.6 (IO35)
RST_RFM95W: U2.31 (IO16), U3.9 (RST)
RX_GPS: U1.6 (RX), U2.23 (TXD0)
SCK_ETHERNET: U2.12 (IO14), U4.4 (SCK)
SCK_RFM95W: U2.28 (IO18), U3.5 (SCK)
SCL: J3.2, J4.2, R4.2, U2.22 (IO22)
SDA: J3.3, J4.3, R3.2, U2.25 (IO21)
TX_GPS: U1.5 (TX), U2.24 (RXD0)

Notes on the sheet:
3V3
GPS
SCL
DIODE
I2C Conn 2
MEASURE INPUT VOLTAGE
LORA RFM95W 915
ESP32
GND
ETHERNET
I2C Conn 1
ESP POWER
DIRECT
SDA
3V3 Linear Regulator
INPUT POWER CONN
EXTRA HEADERS

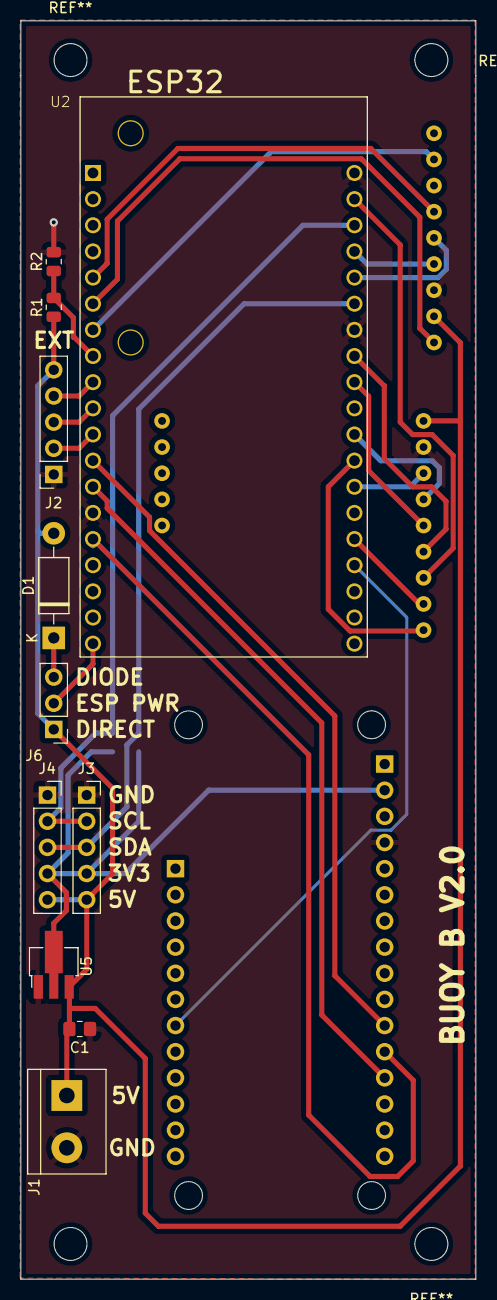
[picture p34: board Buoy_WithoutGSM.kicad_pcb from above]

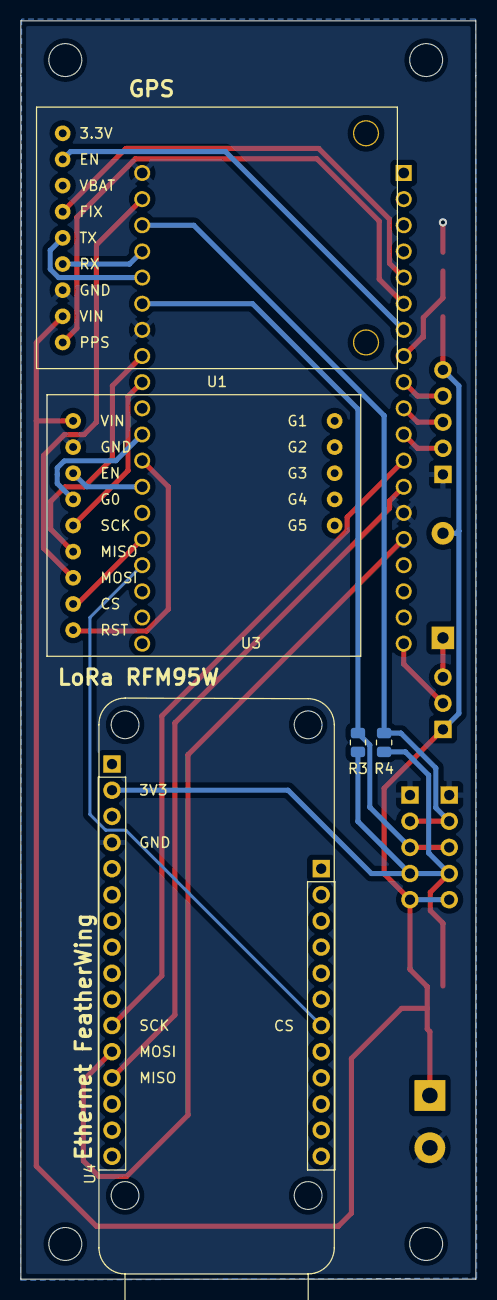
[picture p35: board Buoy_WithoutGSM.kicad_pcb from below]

Board: 2 copper layers, 44.2 x 122.2 mm, 16 parts (4 on the bottom side), 27 nets.

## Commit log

2020-09-28 Added KiCad design
    [Adafruit Ultimate GPS.step, B3B-XH-A.step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]
2020-09-28 Added assembly guide and wiring diagrams
2020-09-28 Added new assembly image
2022-08-16 Updated schematic to Kicad6, removed motor diver and JST Battery connector
    [Buoy_WithoutGSM.kicad_sch]
2022-08-16 Added Ethernet module and input measurement
    [Buoy_WithoutGSM.kicad_sch]
2022-08-16 Added connections to the Extra Conn
    [Adafruit_Feather_Display032x128_000.STEP, Buoy_WithoutGSM.kicad_sch]
2022-08-18 Added 3D model for the Ethernet module and routed changes on PCB
    [12-Pin Header - Male - 2.54mm.step, 16-Pin Header - Male - 2.54mm.step, Buoy_WithoutGSM.kicad_pcb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]
2022-09-02 Changed toutes of the PCB, including routes width
    [Buoy_WithoutGSM.kicad_pcb, Buoy_WithoutGSM.kicad_sch]
2022-09-09 Added gerber files
    [Buoy_WithoutGSM-B_Cu.gbl, Buoy_WithoutGSM-B_Mask.gbs, Buoy_WithoutGSM-B_Paste.gbp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]
2022-09-23 Moved C1 on the PCB, changed PCB shape, moved lower mounting holes
    [Buoy_WithoutGSM.kicad_pcb]
